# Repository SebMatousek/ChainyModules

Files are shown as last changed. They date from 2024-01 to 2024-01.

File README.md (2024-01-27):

# ChainyModules
An ecosystem of electronics modules based on the ESP32-C3FH4 microcontroller capable of chained communication through half-duplex UART.

This project is made to simplify the usage of different modules in robotics projects. Based on the microcontroller ESP32-C3FH4, which is powerfull enough for most tasks, different modules can be created, all the while allowing for chained connection (daisy chaining). Simply put, you can use these modules on different parts of your robot and interconnect them all using only 3 pins, and chain them together that only 1 cable needs to go to the main board (which can be a RPI, one of the modules themselves, ...).

<p align="center">
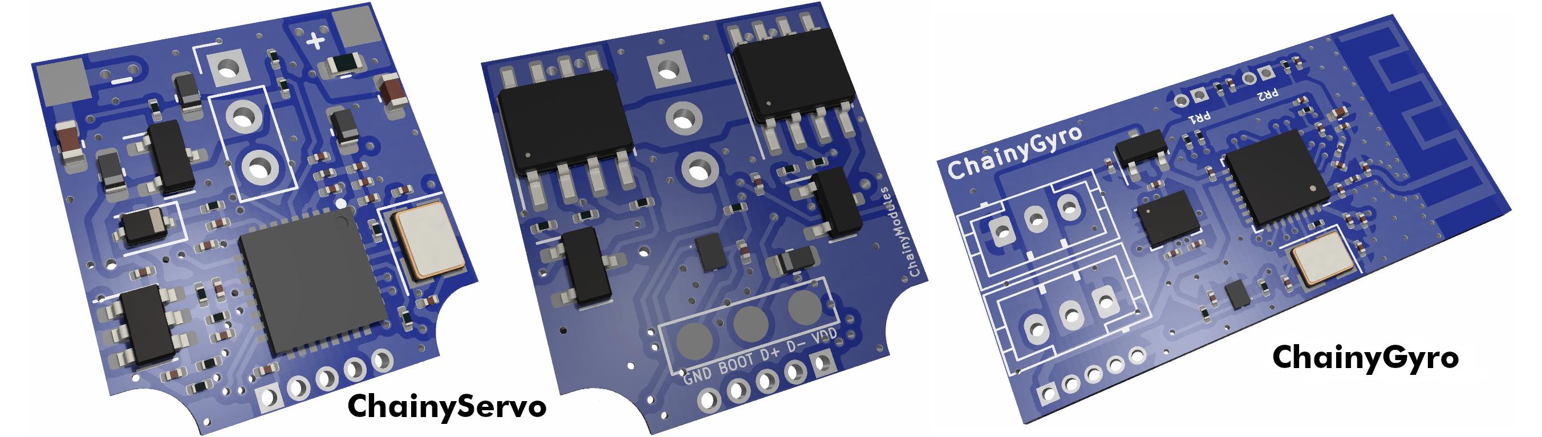
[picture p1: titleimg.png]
   
</p>

Since all the modules use the same microcontroller, the programming is really easy and the communication as well -- the modules use half-duplex UART, the full-duplex UART from the ESP32 is transformed through a dual buffer open drain outputs. The absolute maximum speed for communication is 2,250,000 baud, but its better to use a bit less (1,000,000 baud works great and should be enough for most projects). For the programming of the boards, you can use the programming board specifically designed for this purpose so you don't have to connect 5 pins to each module separatly for programming.

The microcontroller has inbuilt flash for a smaller footprint on the board, and you can use WiFi or Bluetooth with it, it also has flash for storing user variables. It can also be connected to the computer directly without the need of a converter like the CP2102 (you may need to install a driver for it though).

Here are some more parameters:
|Chainy modules|v1.0|
|---|---|
| Microcontroller | ESP32-C3FH4 |
|Supply Voltage|3,3-12V|
|Communication pins|GND, VCC, TX|
|Maximum chained modules (limited by program only)|255|
|Broadcast ID|255|
|Currently designed modules|2|

### Instructions for using already existing modules
The already existing modules have their KiCAD schematic files in the Electronics/ folder. KiCAD 7.0.1 or newer is required, simply open the project and you should be able to plot the gerber files without having to modify anything.

The program is in the folder Software/ and is pretty simple. The basics for each module are the same and are in main.cpp. Every module has to be able to respond to the same basic commands (see table below). Specific modules then have different libraries with code to function. These libraries implement further commands, which have therefore preemptively been be added to the main.cpp switch statement.

|Command|cmd num|
|---|---|
|Set ID|1|
|Read type|2|
|Deepsleep*|3|

*Deepsleep is a command I implemented here because you can (and I did in one of my projects) use the power cables to also charge the robot when not running. Of course, this powers on the modules, so a module recognizes the charging (in my project that was simply using an LED and a photoresistor) and sends this command to the broadcasting address 255, so all the modules turn off. They then consume roughly 5 microamps so it doesn't slow down the charging nearly as much.

### Instructions for the custom servomotors
I created a custom servomotor capable of adressing and reading position, based on the MG90 servomotor. It uses the ChainyServo module board together with the two extension boards located inside the ChainyServo electronics folder. Using the picture in the ChainyServo Electronics folder, you can see how to assemble it. The STL and SLDPRT files are in the Mechanics/ folder. For the gears, motor and potentiometer, you can buy an MG90 (SG90 should work as well) servo and dissassemble it. When soldering the motor to the extension board, be careful that the dot on the plastic bottom of the motor has to align with the white arrow on the board, or the servo will rotate the other way and you will have to change the program. Also, beware that the motor can run on only about 5V, don't burn it - adjust the max pwm output accordingly!

I had my mechanical parts printed at JLCPCB with the material PA12.

#### Troubleshooting the servomotor
If the motor isn't spinning at all, most likely the mechanics is binding somewhere. Try to disassemble to servo and spin the gears manually a bit to see if you can find the problem.
If the motor spins but is going the wrong direction and won't stop jiggling, remove the biggest gear and flip it 180 degrees, which should fix the probelm (it can be inserted into the potentiometer in two ways but only one is correct).

### Instructions for creating a custom module
If you want to create a custom module to go with this repository, you are more than welcome to do so; and if you want send me the files and I can add them here, referencing you (pr not if you don't want me to).

To create a module that will be compatible, you have to mind these things the most:

|Dont't forget this|in your module|
|---|---|
| Microcontroller | ESP32-C3FH4 |
|Supply Voltage|3,3-12V*|
|Communication pins|GND, VCC, TX|
|Connectors|2x JST-PH|
|Programming pins (2mm connector)|VCC D+ D- BOOT GND**|
|Half duplex UART|at least 115 200 baud (ideally just use the buffer I have in my designs)|

*The range can be less if you want, but not more (or else you cannot use the modules already created). Ideally just use a regulator like the one in my modules.
** Or you can put a USB-C connector on the module but that's way too bulky and expensive for my liking.

Other than that, design what you like. You don't have to use my modules at all, as they probably don't fit your needs but that is fine --  the whole point of this project is to provide guidance on how to make such chained modules and to have some code and electronics done for it already, and over time hopefully create a whle ecosystem of these modules so that anyone can se what others have already designed and pick what souits them best. Have fun making, makers!

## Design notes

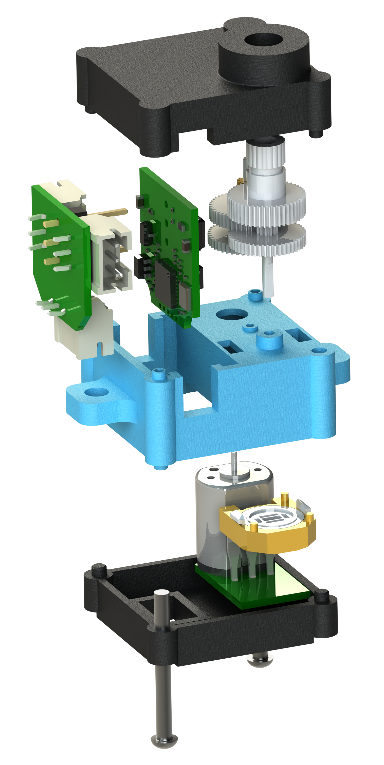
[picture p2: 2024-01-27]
Electronics/ChainyServo/ChainyServo_exploded_view.png

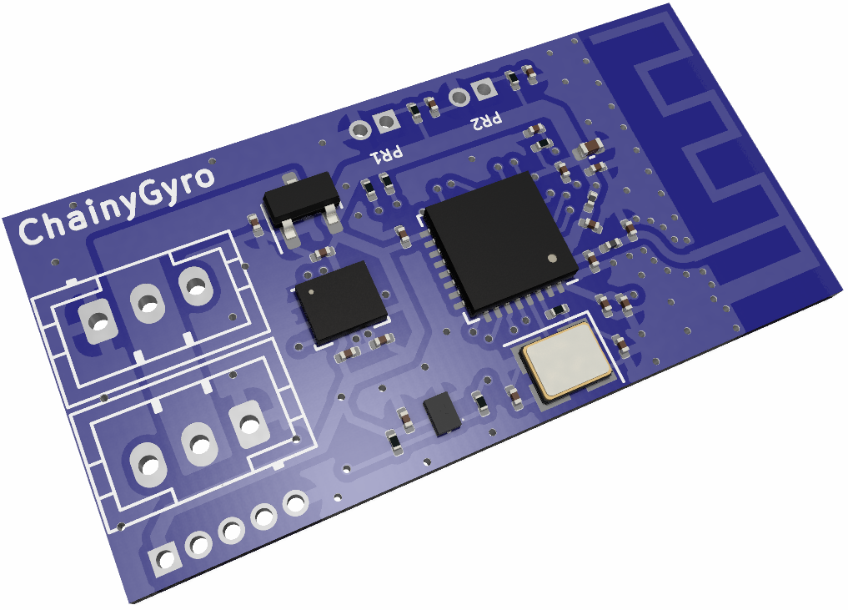
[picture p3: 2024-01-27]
chainygyro.png

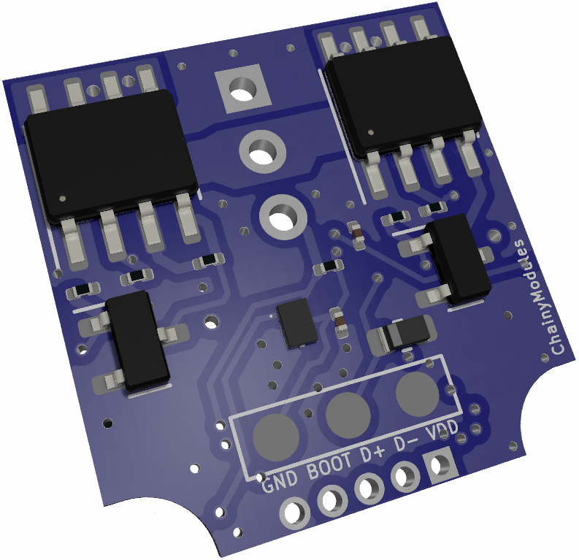
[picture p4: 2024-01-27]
chainyservo_bottom.png

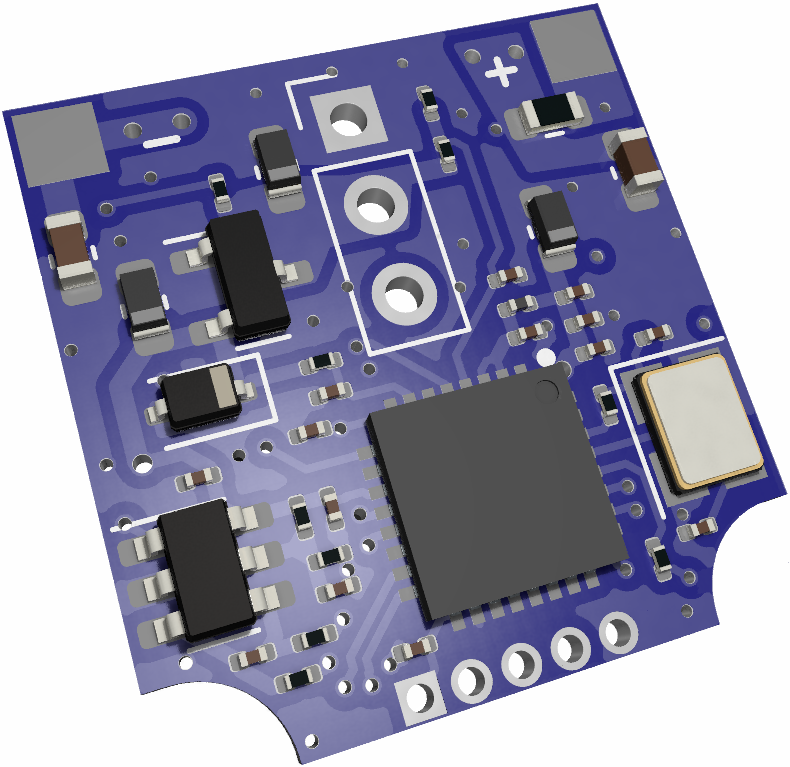
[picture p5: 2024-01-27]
chainyservo.png

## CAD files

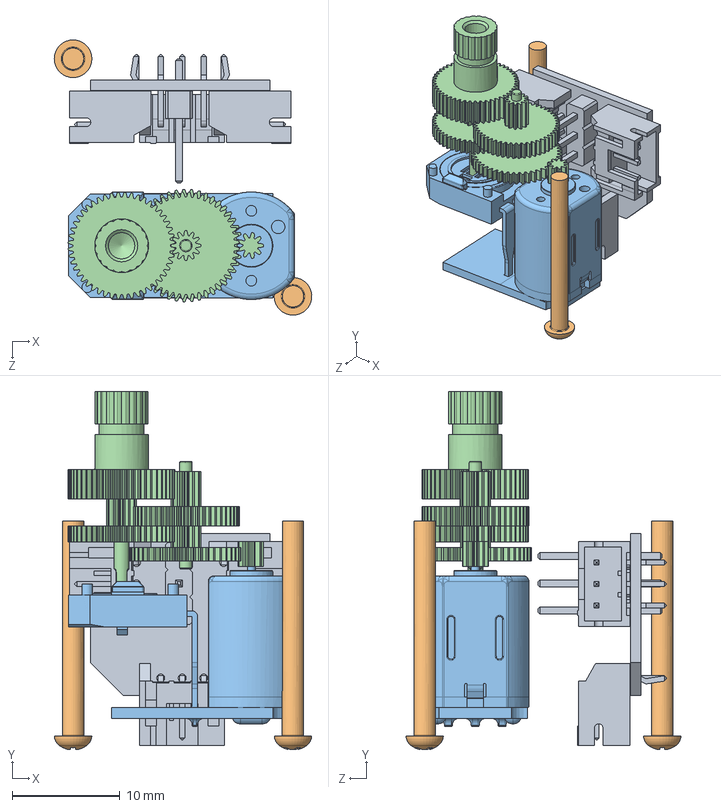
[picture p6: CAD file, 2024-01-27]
Electronics/ChainyServo/Mechanics/AssemChainyServo.SLDASM
23.9 x 33.3 x 25.6 mm
ConnectorAdapterBoard
Screw x 2
Motor
Gears

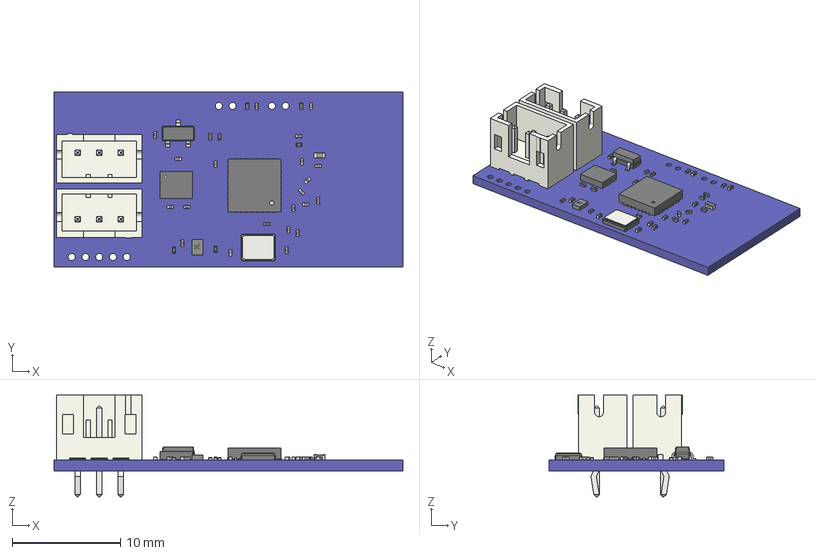
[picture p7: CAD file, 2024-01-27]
Electronics/ChainyGyro/chainygyro.step
32.2 x 16.2 x 9.40 mm
Pcb_cac2
R5_R_0201_0603Metric_ae45ce2bcee0 x 8
C15_C_0201_0603Metric_2e5032d23c7a x 18
L2_L_0201_0603Metric_8c112b5ab684 x 2
U1_SOT_23_ce7e2b68684f
U2_LGA_14_3x25mm_P05mm_LayoutBorder3x4y_143f698fa12f
J1_JST_B3B_PH_K_fbf7c7734919 x 2
C2_C_0402_1005Metric_e228e85d4d95
IC1_QFN_32_1EP_5x5mm_P05mm_EP31x31mm_5082fcadb45d
SOT886 Mold Body
Y1_Crystal_SMD_3225-4Pin_3.2x2.5mm_c7b0457659bb

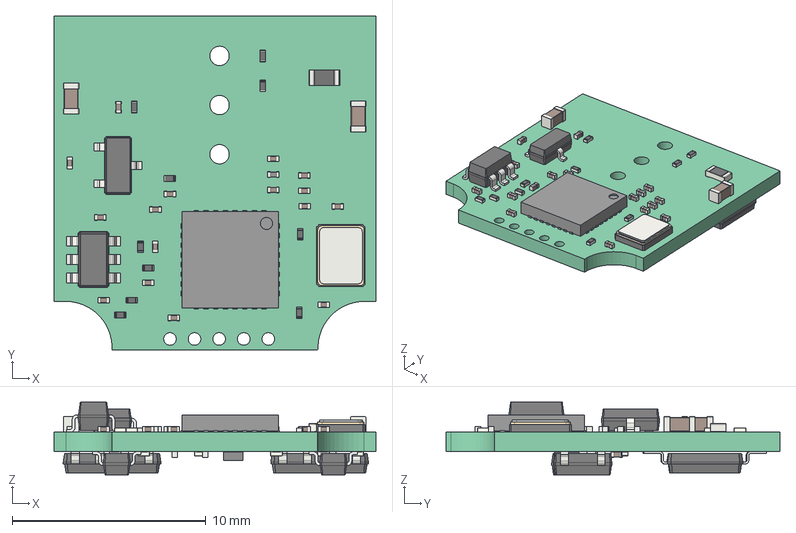
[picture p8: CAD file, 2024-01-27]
Electronics/ChainyServo/chainyservo.step
16.6 x 17.2 x 3.75 mm
Pcb_7fa7
C19_C_0201_0603Metric_a312519759b9 x 18
R10_R_0201_0603Metric_ce88abe40c4e x 16
L1_L_0201_0603Metric_373e583e6430
R13_R_0603_1608Metric_193286fe7f68
C4_C_0603_1608Metric_0fb439af5e9e x 2
U5_SOT_23_6_acd867c84d74
ThermalPin
PinsArrayLR
PinsArrayLR001
PinsArrayLR002
PinsArrayLR003
PinsArrayLR004
PinsArrayLR005
PinsArrayLR006
PinsArrayLR007
PinsArrayLR008
PinsArrayLR009
PinsArrayLR010
PinsArrayLR011
PinsArrayLR012
PinsArrayLR013
PinsArrayLR014
PinsArrayLR015
PinsArrayTB
PinsArrayTB001
PinsArrayTB002
PinsArrayTB003
PinsArrayTB004
PinsArrayTB005
PinsArrayTB006
PinsArrayTB007
PinsArrayTB008
PinsArrayTB009
PinsArrayTB010
PinsArrayTB011
PinsArrayTB012
PinsArrayTB013
PinsArrayTB014
PinsArrayTB015
U4_SOT_23_8388c0d6ca76 x 3
Y1_Crystal_SMD_3225-4Pin_3.2x2.5mm_989cafc28578
SOT886 Mold Body
U1_SSOP_8_39x505mm_P127mm_962db2c4c331[2] x 2

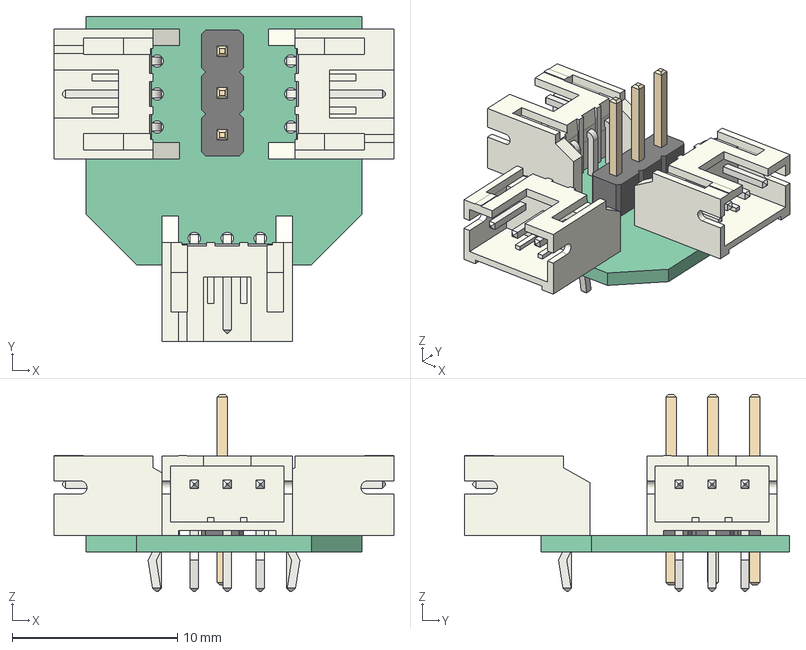
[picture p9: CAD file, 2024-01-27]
Electronics/ChainyServo/Extension_boards/ConnectorAdapter/connectoradapter.step
20.6 x 19.7 x 11.9 mm
Pcb_ee37
J1_PinHeader_1x03_P254mm_Vertical_d5cdea604e18
J4_JST_S3B_PH_K_1e32457ae4c8 x 3

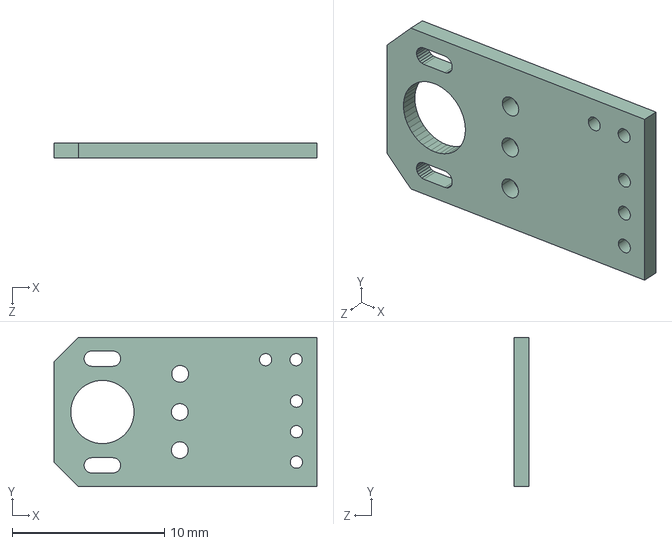
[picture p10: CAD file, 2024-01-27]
Electronics/ChainyServo/Extension_boards/MotorAdapter/motoradapter.step
17.2 x 9.80 x 0.98 mm

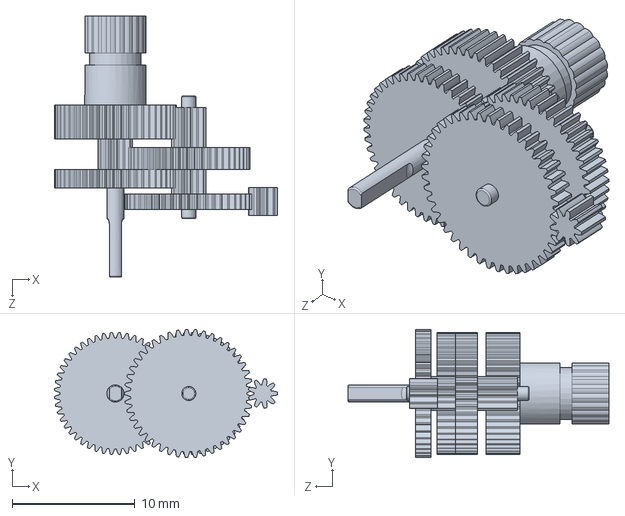
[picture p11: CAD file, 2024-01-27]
Electronics/ChainyServo/Mechanics/Gears.SLDPRT
18.2 x 10.5 x 21.2 mm

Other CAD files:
Electronics/ChainyServo/Mechanics/Body.SLDPRT
Electronics/ChainyServo/Mechanics/Bottom.SLDPRT
Electronics/ChainyServo/Mechanics/Top.SLDPRT
Electronics/ChainyServo/Mechanics/ConnectorAdapterBoard.SLDPRT
Electronics/ChainyServo/Mechanics/Motor.SLDPRT
Electronics/ChainyServo/Mechanics/Screw.SLDPRT
Electronics/ChainyServo/Extension_boards/MotorAdapter/motoradapter.STL

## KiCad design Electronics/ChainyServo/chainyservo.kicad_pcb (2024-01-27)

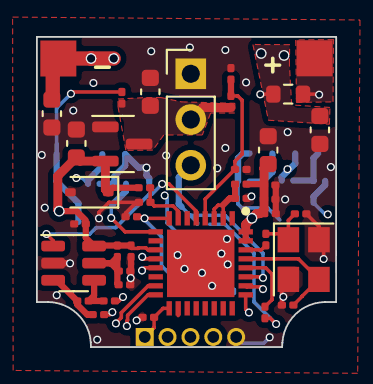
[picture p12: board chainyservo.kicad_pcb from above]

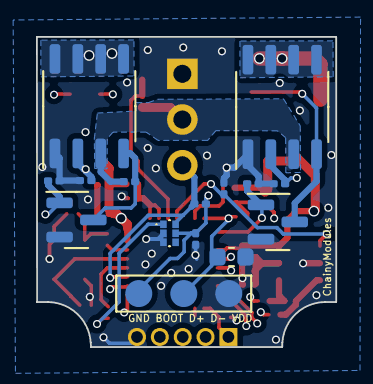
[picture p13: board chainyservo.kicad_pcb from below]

Board: 4 copper layers, 16.6 x 17.2 mm, 55 parts (15 on the bottom side), 29 nets.

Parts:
C1, C2, C7, C8, C9, C10, C13, C14, C17, C18, C19, C20: 100nF; C_0201_0603Metric
C3, C4: 27nF; C_0603_1608Metric
C5, C6, C21, C22: 2.2uF; C_0603_1608Metric
C11: 10nF; C_0201_0603Metric
C12: 1uF; C_0201_0603Metric
C15, C16: 16pF; C_0201_0603Metric
D1: BSD3C031V; D_SOD-323
IC1: ESP32-C3FH4; QFN50P500X500X90-33N-D
IC2: 74LVC2G07GM,132; PESD3V3L5UF115
J1: M+; Conn_pad_2x2mm
J2: Conn_01x03_Female; Pad_3_potentiometer
J3: Conn_01x03_Female; PinHeader_1x03_P2.54mm_Vertical
J4: Conn_01x05_Female; PinHeader_1x05_P1.27mm_Vertical
J5: M-; Conn_pad_2x2mm
L1: 2nH; L_0201_0603Metric
Q1, Q2: BSS138; SOT-23
R1, R3: 1k; R_0201_0603Metric
R2, R4, R5, R6, R10, R11, R15, R19: 22k; R_0201_0603Metric
R7: 10k; R_0201_0603Metric
R12, R14: 33R; R_0201_0603Metric
R13: 68m; R_0603_1608Metric
R16: 7k5; R_0201_0603Metric
R17: 0R; R_0201_0603Metric
R18: 499R; R_0201_0603Metric
U1, U2: WSP4606A; SOP-8_3.9x4.9mm_P1.27mm
U4: H7233-1; SOT-23
U5: INA181A1IDBVR; SOT-23-6
Y1: Crystal_GND23; Crystal_SMD_3225-4Pin_3.2x2.5mm

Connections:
+3V3: C2.1, C6.1, C9.1, C10.1, C11.1, C12.1, C13.1, C18.1, C21.1, D1.1 (K), IC1.11 (VDD3P3_RTC), IC1.17 (VDD3P3_CPU), IC1.31 (VDDA_1), IC1.32 (VDDA_2), IC2.5 (VCC), J2.1, J4.1, L1.1, R7.2, R10.1, R19.2, U4.2 (VO), U5.6 (V+)
AG1: IC1.9 (MTMS), Q1.1 (G), R5.1
AG2: IC1.16 (GPIO10), Q2.1 (G), R6.1
AMP: C20.1, IC1.5 (XTAL_32K_N), U5.1
BOOT: IC1.15 (GPIO9), J4.4
G1: Q1.3 (D), R1.2, U1.4 (G1)
G2: IC1.12 (MTCK), R2.1, U1.2 (G2)
G3: Q2.3 (D), R3.2, U2.4 (G1)
G4: IC1.13 (MTDO), R4.1, U2.2 (G2)
GND: C1.2, C2.2, C3.2, C4.2, C5.2, C6.2, C7.2, C9.2, C10.2, C11.2, C12.2, C13.2, C14.2, C15.2, C16.2, C17.2, C18.2, C19.2, C20.2, C21.2, C22.2, D1.2 (A), IC1.33 (GND), IC2.2 (GND), IC2.3 (2A), J2.3, J3.1, J4.5, Q1.2 (S), Q2.2 (S), R2.2, R4.2, R5.2, R6.2, R11.2, R16.2, U1.1 (S2), U2.1 (S2), U4.1 (GND), U5.2 (GND), Y1.2, Y1.4
M+: C4.1, R12.2, R13.1, U2.5 (D1), U2.6 (D1), U2.7 (D2), U2.8 (D2)
M-: C3.1, J5.1, U1.5 (D1), U1.6 (D1), U1.7 (D2), U1.8 (D2)
unnamed: C15.1, R17.2, Y1.1
unnamed: C17.1, IC1.7 (CHIP_EN), R19.1
unnamed: C14.1, IC1.2 (VDD3P3_1), IC1.3 (VDD3P3_2), L1.2
unnamed: IC2.1 (1A), R18.2
unnamed: J1.1, R13.2, R14.2
unnamed: C8.2, R14.1, U5.3 (+)
unnamed: C8.1, R12.1, U5.4 (-)
POT: C19.1, C22.1, IC1.8 (GPIO3), J2.2
REF: C7.1, R10.2, R11.1, U5.5 (REF)
RX: IC1.27 (U0RXD), IC2.6 (1Y), J3.3, R7.1
TX: IC1.28 (U0TXD), R18.1
USB_D+: IC1.26 (GPIO19), J4.2
USB_D-: IC1.25 (GPIO18), J4.3
VIN: C5.1, J3.2, R1.1, R3.1, R15.1, U1.3 (S1), U2.3 (S1), U4.3 (VI)
VM: C1.1, IC1.4 (XTAL_32K_P), R15.2, R16.1
XTAL_N: C16.1, IC1.29 (XTAL_N), Y1.3
XTAL_P: IC1.30 (XTAL_P), R17.1

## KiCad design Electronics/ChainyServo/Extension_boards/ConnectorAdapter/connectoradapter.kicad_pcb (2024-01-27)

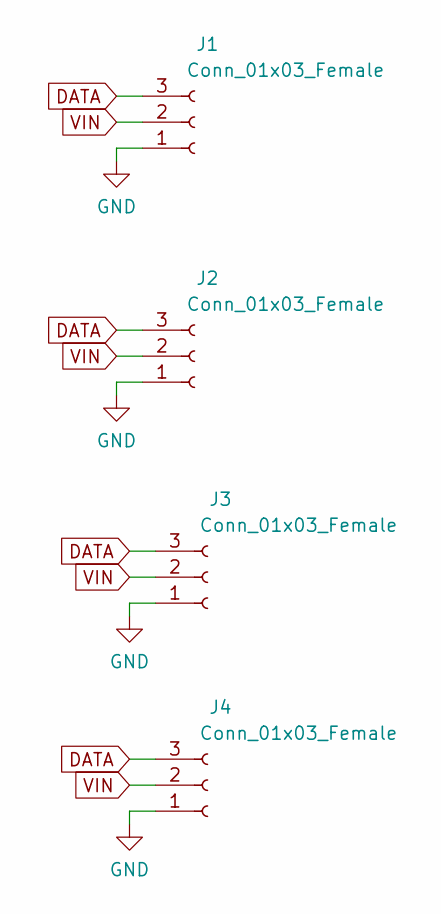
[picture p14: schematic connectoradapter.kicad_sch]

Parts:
J1: Conn_01x03_Female; PinHeader_1x03_P2.54mm_Vertical
J2, J3, J4: Conn_01x03_Female; JST_PH_S3B-PH-K_1x03_P2.00mm_Horizontal

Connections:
DATA: J1.3, J2.3, J3.3, J4.3
GND: J1.1, J2.1, J3.1, J4.1
VIN: J1.2, J2.2, J3.2, J4.2

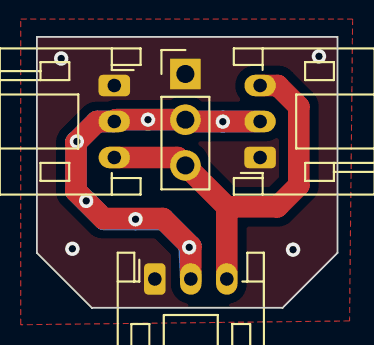
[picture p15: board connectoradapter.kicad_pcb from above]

Board: 4 copper layers, 16.7 x 15.0 mm, 4 parts (0 on the bottom side), 3 nets.

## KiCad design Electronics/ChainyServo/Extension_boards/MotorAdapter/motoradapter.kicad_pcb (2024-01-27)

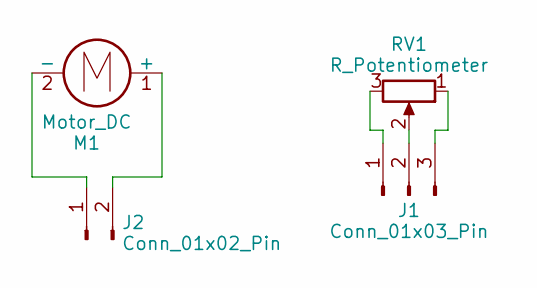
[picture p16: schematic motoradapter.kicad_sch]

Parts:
J1: Conn_01x03_Pin; PinHeader_1x03_P2.00mm_Vertical
J2: Conn_01x02_Pin; PinHeader_1x02_P2.00mm_Vertical
M1: Motor_DC; MG90I_motor
RV1: R_Potentiometer; MG90I_potentiometer

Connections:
unnamed: J1.1, RV1.3
unnamed: J1.2, RV1.2
unnamed: J1.3, RV1.1
unnamed: J2.1, M1.2 (-)
unnamed: J2.2, M1.1 (+)

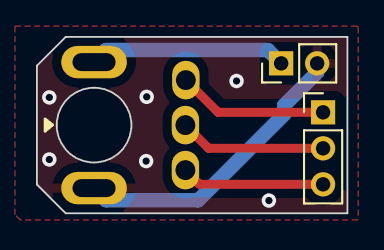
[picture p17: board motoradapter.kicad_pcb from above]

Board: 4 copper layers, 17.2 x 9.8 mm, 4 parts (0 on the bottom side), 5 nets.

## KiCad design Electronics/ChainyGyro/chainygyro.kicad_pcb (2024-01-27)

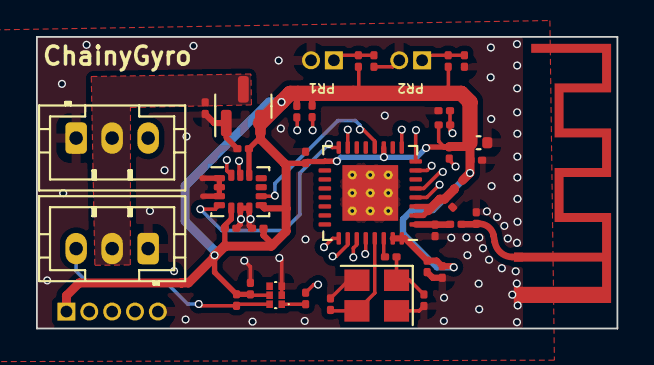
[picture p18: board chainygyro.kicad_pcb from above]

Board: 4 copper layers, 32.2 x 16.2 mm, 40 parts (0 on the bottom side), 22 nets.

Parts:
AE1: PCB Antenna 2.4GHz 50Ohm; Texas_SWRA117D_2.4GHz_Left
C1, C3, C4, C6, C7, C12, C14, C17, C18, C19: 100nF; C_0201_0603Metric
C2: 10uF; C_0402_1005Metric
C5, C8: 16pF; C_0201_0603Metric
C9, C15, C16: 1uF; C_0201_0603Metric
C10: 10nF; C_0201_0603Metric
C11, C13: 3.3pF; C_0201_0603Metric
IC1: ESP32-C3FH4; QFN-32-1EP_5x5mm_P0.5mm_EP3.1x3.1mm_ThermalVias
IC2: 74LVC2G07GM,132; PESD3V3L5UF115
J1, J2: Conn_01x03_Female; JST_PH_B3B-PH-K_1x03_P2.00mm_Vertical
J3: Conn_01x05_Female; PinHeader_1x05_P1.27mm_Vertical
J4, J5: Conn_01x02_Socket; PinHeader_1x02_P1.27mm_Vertical
L1: 2nH; L_0201_0603Metric
L2: 2.2nH; L_0201_0603Metric
R1: 0R; R_0201_0603Metric
R2: 22k; R_0201_0603Metric
R3, R4, R6, R7, R8: 10k; R_0201_0603Metric
R5: 499R; R_0201_0603Metric
U1: H7233-1; SOT-23
U2: LSM6DS3TR-C; LGA-14_3x2.5mm_P0.5mm_LayoutBorder3x4y
Y1: Crystal_GND23; Crystal_SMD_3225-4Pin_3.2x2.5mm

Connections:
+3V3: C2.1, C4.1, C9.1, C10.1, C12.1, C14.1, C16.1, C17.1, C18.1, C19.1, IC1.11 (VDD3P3_RTC), IC1.17 (VDD3P3_CPU), IC1.31 (VDDA_1), IC1.32 (VDDA_2), IC2.5 (VCC), J3.1, L1.1, R2.2, R3.1, R4.1, R6.2, R7.1, R8.1, U1.2 (VO), U2.5 (VDDIO), U2.8 (VDD), U2.12 (CS)
BOOT: IC1.15 (GPIO9), J3.4
GND: AE1.1, C1.2, C2.2, C3.2, C4.2, C5.2, C6.2, C7.2, C8.2, C9.2, C10.2, C11.2, C12.2, C13.2, C14.2, C15.2, C16.2, C17.2, C18.2, C19.2, IC1.33 (GND), IC2.2 (GND), IC2.3 (2A), J1.1, J2.1, J3.5, J4.2, J5.2, U1.1 (GND), U2.1 (SDO/SA0), U2.2 (SDX), U2.3 (SCX), U2.6 (GND), U2.7 (GND), Y1.2, Y1.4
INT1: IC1.16 (GPIO10), U2.4 (INT1)
INT2: IC1.12 (MTCK), U2.9 (INT2)
LNA: C11.1, IC1.1 (LNA_IN), L2.1
unnamed: AE1.2, C13.1, L2.2
unnamed: C5.1, R1.2, Y1.1
unnamed: C7.1, IC1.7 (CHIP_EN), R2.1
unnamed: C6.1, IC1.2 (VDD3P3_1), IC1.3 (VDD3P3_2), L1.2
unnamed: IC2.1 (1A), R5.2
PR1: C1.1, IC1.9 (MTMS), J5.1, R4.2
PR2: C3.1, IC1.8 (GPIO3), J4.1, R3.2
RX: IC1.27 (U0RXD), IC2.6 (1Y), J1.3, J2.3, R6.1
SCL: IC1.4 (XTAL_32K_P), R7.2, U2.13 (SCL)
SDA: IC1.5 (XTAL_32K_N), R8.2, U2.14 (SDA)
TX: IC1.28 (U0TXD), R5.1
USB_D+: IC1.26 (GPIO19), J3.2
USB_D-: IC1.25 (GPIO18), J3.3
VIN: C15.1, J1.2, J2.2, U1.3 (VI)
XTAL_N: C8.1, IC1.29 (XTAL_N), Y1.3
XTAL_P: IC1.30 (XTAL_P), R1.1

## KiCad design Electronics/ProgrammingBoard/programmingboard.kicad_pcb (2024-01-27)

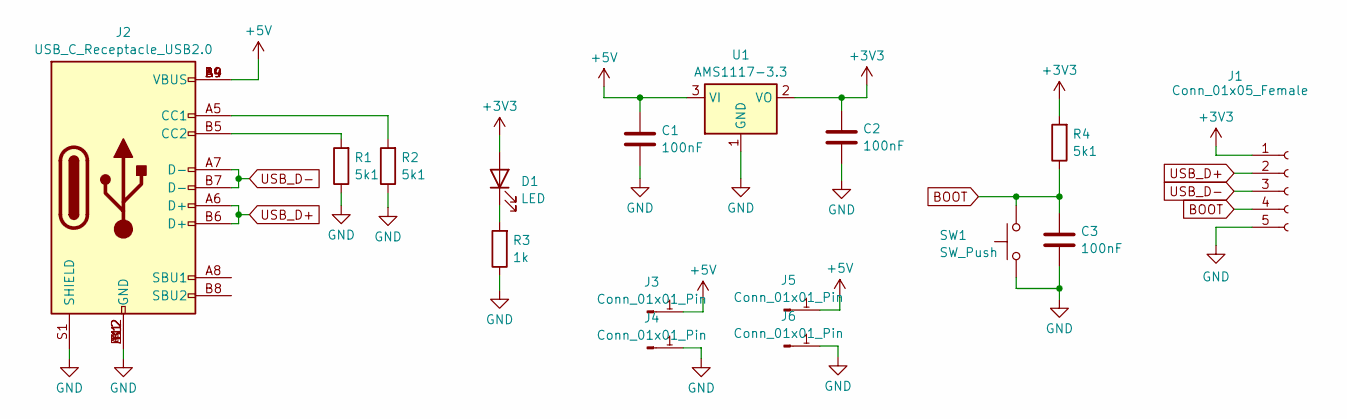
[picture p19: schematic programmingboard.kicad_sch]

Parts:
C1, C2, C3: 100nF; C_1206_3216Metric_Pad1.33x1.80mm_HandSolder
D1: LED; D_1206_3216Metric_Pad1.42x1.75mm_HandSolder
J1: Conn_01x05_Female; PinHeader_1x05_P1.27mm_Vertical
J2: USB_C_Receptacle_USB2.0; USB_C_Receptacle_GCT_USB4105-xx-A_16P_TopMnt_Horizontal; LCSC C393939
J3, J4, J5, J6: Conn_01x01_Pin; PinHeader_1x01_P2.54mm_Vertical
R1, R2, R4: 5k1; R_1206_3216Metric_Pad1.30x1.75mm_HandSolder
R3: 1k; R_1206_3216Metric_Pad1.30x1.75mm_HandSolder
SW1: SW_Push; SW_PUSH_6mm_H5mm
U1: AMS1117-3.3; SOT-223-3_TabPin2

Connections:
+3V3: C2.1, D1.2 (A), J1.1, R4.2, U1.2 (VO)
+5V: C1.1, J2.A4 (VBUS), J2.A9 (VBUS), J2.B4 (VBUS), J2.B9 (VBUS), J3.1, J5.1, U1.3 (VI)
BOOT: C3.1, J1.4, R4.1, SW1.2
GND: C1.2, C2.2, C3.2, J1.5, J2.A1 (GND), J2.A12 (GND), J2.B1 (GND), J2.B12 (GND), J2.S1 (SHIELD), J4.1, J6.1, R1.1, R2.1, R3.1, SW1.1, U1.1 (GND)
unnamed: D1.1 (K), R3.2
unnamed: J2.A5 (CC1), R2.2
unnamed: J2.B5 (CC2), R1.2
USB_D+: J1.2, J2.A6 (D+), J2.B6 (D+)
USB_D-: J1.3, J2.A7 (D-), J2.B7 (D-)

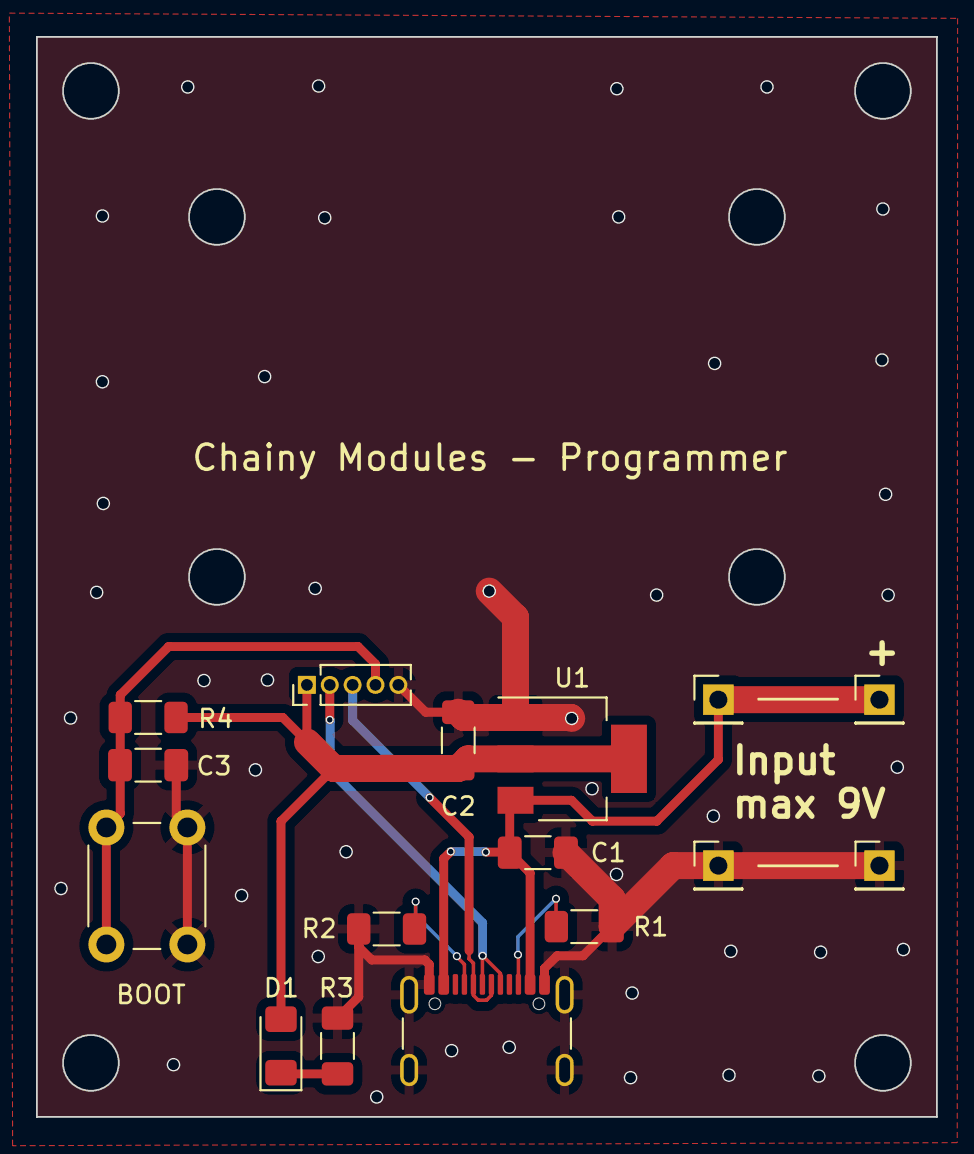
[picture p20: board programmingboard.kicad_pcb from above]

Board: 2 copper layers, 50.0 x 60.0 mm, 16 parts (0 on the bottom side), 9 nets.

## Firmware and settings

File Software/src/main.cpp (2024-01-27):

#include <Arduino.h>
#include <EEPROM.h>
#include "chainyservo.h"
#include "chainygyro.h"

CHAINY_SERVO *s;
CHAINY_GYRO *g;

#define SERIAL_SPEED 1000000 // 1,000,000 baud; if changed, dont forget to changed Serial.setTimeout() as well, see void setup for more info
#define EEPROM_SIZE 10

#define CHARGING_GUARD_ID -1 // the id of the chainy_gyro board that monitors wireless charging through power cables and sends the deepsleep command

/* EEPROM map
0 ... ID
1 ... MODULE_TYPE

(for CHAINY_SERVO)
5 ... UPPER_LIMIT_H 
6 ... UPPER_LIMIT_L
7 ... LOWER_LIMIT_H
8 ... LOWER_LIMIT_L
*/

uint8_t ID;
uint8_t MODULE_TYPE;

//MODULE_TYPES:
#define DEFAULT_MODULE 0
#define CHS 1 //Chainy servo
#define CHG 3 // Chainy gyro

byte buff[8]; // [\x55][\xID][\xCOMMAND][\xDATA1][\xDATA2][\xDATA3][\xDATA4][\xCHECKSUM] this is the structure of th recieved data
byte send_buff[6]; // [\x55][\xID][\xCOMMAND][\xDATA1][\xDATA2][\xCHECKSUM] // this is the structure of the sent data

/*COMMAND LIST (for default module)
1 ... ID_WRITE
2 ... TYPE_READ
*/

TaskHandle_t Move;

uint8_t perform_checksum()
{
  int sum = 0;
  for(int i = 0; i < sizeof(send_buff); i++)
  {
    sum += send_buff[i];
    if(sum > 255) sum -= 256;
  }

  return uint8_t(sum);
}

void clear_buffer()
{
  for(int i = 0; i < sizeof(buff); i++)
  {
    buff[i] = 0;
  }
}

void send_packet(uint8_t cmd, uint8_t data1, uint8_t data2 = 0)
{
  send_buff[0] = byte(85);
  send_buff[1] = byte(ID);
  send_buff[2] = byte(cmd);
  send_buff[3] = byte(data1);
  send_buff[4] = byte(data2);
  send_buff[5] = byte(perform_checksum());

  Serial.write(send_buff, sizeof(send_buff));
}

void send_packet_discombine(uint8_t cmd, uint16_t data)
{
  int upper = data / 100;
  int lower = data - upper*100;

  send_packet(cmd, upper, lower);
}

void send_packet_int(uint8_t cmd, int16_t data)
{
  int upper, lower;

  if(data >= 0)
  {
    data += 10000;
    upper = data / 100;
    lower = data - upper*100;
  }
  else
  {
    data = abs(data);
    upper = data / 100;
    lower = data - upper*100;
  }

  send_packet(cmd, upper, lower);
}

void id_write(uint8_t id)
{
  ID = id;
  EEPROM.write(0, ID);
    EEPROM.commit();
}

void type_read()
{
  send_packet(2, MODULE_TYPE);
}

void hibernate() {
    esp_sleep_pd_config(ESP_PD_DOMAIN_RTC_PERIPH,   ESP_PD_OPTION_OFF);
    esp_sleep_pd_config(ESP_PD_DOMAIN_RTC_SLOW_MEM, ESP_PD_OPTION_OFF);
    esp_sleep_pd_config(ESP_PD_DOMAIN_RTC_FAST_MEM, ESP_PD_OPTION_OFF);
    esp_sleep_pd_config(ESP_PD_DOMAIN_XTAL,         ESP_PD_OPTION_OFF);
    esp_deep_sleep_start();
}

void send_all_deepsleep()
{
  send_buff[0] = byte(85);
  send_buff[1] = byte(255);
  send_buff[2] = byte(3);
  send_buff[3] = byte(0);
  send_buff[4] = byte(0);
  send_buff[5] = byte(perform_checksum());

  Serial.write(send_buff, sizeof(send_buff));
  hibernate();
}

void command_central(uint8_t command, uint8_t data1, uint8_t data2, uint8_t data3, uint8_t data4)
{
  switch(command)
  {
  case 1:
    id_write(data1);
    break;

  case 2:
    type_read();
    break;

  case 3:
    hibernate(); // hibernation for when charging over power cables
    break;

  case 10:
    if(MODULE_TYPE == CHS) s->move(data1, data2, data3);
    break;

  case 11:
    if(MODULE_TYPE == CHS) s->move_wait(data1, data2, data3);
    break;

  case 12:
    if(MODULE_TYPE == CHS) s->move_start();
    break;

  case 13:
    if(MODULE_TYPE == CHS) send_packet_discombine(13, s->vin_read());
    break;

  case 14:
    if(MODULE_TYPE == CHS) send_packet_discombine(14, s->pos_read());
    break;

  case 15:
    if(MODULE_TYPE == CHS) 
    {
      uint8_t u_h;
      uint8_t u_l;
      uint8_t l_h;
      uint8_t l_l;
      uint16_t u;
      uint16_t l;

      s->limit_write(data1, data2, data3, data4);

      u = s->upper_limit_read();
      l = s->lower_limit_read();

      u_h = u/100;
      u_l = u-u_h*100;
      l_h = l/100;
      l_l = l-l_h*100;

      EEPROM.write(5, u_h);
      EEPROM.write(6, u_l);
      EEPROM.write(7, l_h);
      EEPROM.write(8, l_l);
        EEPROM.commit();
    }
    break;

  case 16:
    if(MODULE_TYPE == CHS) send_packet_discombine(16, s->upper_limit_read());
    break;

  case 17:
    if(MODULE_TYPE == CHS) send_packet_discombine(17, s->lower_limit_read());
    break;

  case 18:
    if(MODULE_TYPE == CHS) s->blocking_write(bool(data1));
    break;

  case 19:
    if(MODULE_TYPE == CHS) send_packet(19, s->blocking_read());
    break;

  case 20:
    if(MODULE_TYPE == CHS) send_packet_int(20, s->current_read());
    break;

  case 30:
    if(MODULE_TYPE == CHG) g->get_acceleration();
    break;

  case 31:
    if(MODULE_TYPE == CHG) g->get_gyro();
    break;

  case 32:
    if(MODULE_TYPE == CHG) g->get_temperature();
    break;

  case 33:
    if(MODULE_TYPE == CHG) send_packet_discombine(33, g->pr1());
    break;

  case 34:
    if(MODULE_TYPE == CHG) send_packet_discombine(34, g->pr2());
    break;
  }
}

bool check_checksum()
{
  int sum = 0;
  for(int i = 0; i < sizeof(buff)-1; i++)
  {
    sum += buff[i];
    if(sum > 255) sum -= 256;
  }

  if(sum == buff[sizeof(buff)-1]) return true;
  return false;
}

int parse_command()
{
  if(!check_checksum()) return -3;
  if(!(buff[0] == byte('\x55'))) return -1;
  if(!(buff[1] == ID || buff[1] == 255)) return -2; // check if id is mine or if this is a broadcast

  command_central(buff[2], buff[3], buff[4], buff[5], buff[6]);
  clear_buffer();
  return 0;
}

void driveServo(void *p)
{
  if(MODULE_TYPE == CHS) s->moveLoop();
}

void monitorCharging()
{
  attachInterrupt(PR2_PIN, send_all_deepsleep, FALLING);
}

void setup()
{
  clear_buffer();
  Serial.begin(SERIAL_SPEED);
  Serial.setTimeout(2); // set the timeout for UART communication, without this line the ESP32 will wait 1s. Minimum recommended is 2ms at 1,000,000 baud, 30ms at 115,200 baud

  while(Serial.available() > 0) Serial.read(); //clear serial buffer

  EEPROM.begin(EEPROM_SIZE);
  
  ID = EEPROM.read(0); //if 255, the ID was never set; set ID to 0-254, default is 0, but it will be set only in this runthrough, not saved to flash
  if(ID == 255) ID = 0;

  MODULE_TYPE = EEPROM.read(1); //if 255, the MODULE_TYPE was never set; set MODULE_TYPE manually according to the table above, and write to flash
  if(MODULE_TYPE == 255)
  {
    MODULE_TYPE = 0;
    EEPROM.write(1, MODULE_TYPE);

    if(MODULE_TYPE == CHS)
    {
      EEPROM.write(5, 10);
      EEPROM.write(6, 0);
      EEPROM.write(7, 0);
      EEPROM.write(8, 0);
    }

    EEPROM.commit();
  }

  if(MODULE_TYPE == CHS)
  {
    uint8_t u_h = EEPROM.read(5);
    uint8_t u_l = EEPROM.read(6);
    uint8_t l_h = EEPROM.read(7);
    uint8_t l_l = EEPROM.read(8);

    s = new CHAINY_SERVO(u_h*100+u_l, l_h*100+l_l);

    xTaskCreatePinnedToCore(driveServo, "_move", 10000, NULL, 0, &Move, 1);
  }
  else if(MODULE_TYPE = CHG)
  {
    g = new CHAINY_GYRO(ID);

    if(ID == CHARGING_GUARD_ID) monitorCharging();
  }
}

void loop()
{
  if(Serial.available() > 0)
  {
    Serial.readBytes(buff, 8);
    parse_command();
  }
  delay(2);
}
